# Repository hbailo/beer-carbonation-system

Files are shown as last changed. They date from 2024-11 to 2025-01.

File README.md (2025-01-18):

# Sistema de carbonatación de cerveza

## Alumno
Hernán Leandro Bailo

## Resumen
Se describe el desarrollo de la automatización de un sistema de carbonatación de cerveza en barriles.

El sistema se basa en una placa de desarrollo NUCLEO-F429ZI y esta diseñado conforme a los patrones de
diseño de procesos modulares de ISA S88.

Entre sus funcionalidades principales se incluye el control mediante HMI de la receta de carbonatación, per-
mitiendo al operador iniciar, detener y reanudar su ejecución, el monitoreo y control mediante una computadora
de supervisión y el acceso a los datos de procesos desde un navegador web.

El sistema destaca por su capacidad para mejorar la consistencia en la calidad del producto final, optimizando
el tiempo de operación y minimizando la intervención manual. Su diseño modular y escalable lo convierte en una
solución adaptable para diferentes escalas de producción en la industria cervecera.

## Descripción del proceso
En el proceso de elaboración de cerveza una de las últimas etapas es la carbonatación, donde se incorpora
dióxido de carbono a lı́quido para crear efervescencia, realzar el sabor, conservar la cerveza y otros propósitos.
En el caso actual la carbonatación se realiza artificialmente mediante la incorporación forzada del gas.

El diagrama P&ID del sistema de carbonatación se muestra a continuación. Los tags utilizados están en formato IEC 81346 [1].

El sistema consiste en untanque de CO2 conectado a un barril de cerveza a través de la válvula solenoide
QMB1. El barril se encuentra montado sobre una criba vibratoria que se acciona mediante el motor eléctrico
MAA1. La presión interna del barril se mide con el transmisor BPA1.

<picture>
    <source media="(prefers-color-scheme: dark)" srcset="doc/architecture/process-and-instrumentation-diagram-dark.png">
    <source media="(prefers-color-scheme: light)" srcset="doc/architecture/process-and-instrumentation-diagram-light.png"> 
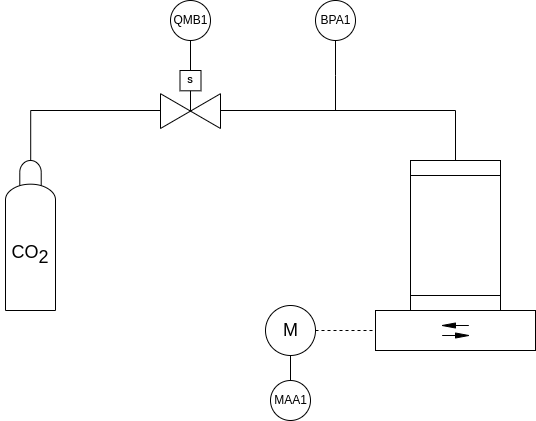
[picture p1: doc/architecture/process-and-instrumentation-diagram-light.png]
Shows the recipe state diagram.
    
</picture>

### Fases del proceso
El procedimiento de carbonatación se basa en la iteración de las siguientes dos fases, estructuradas según el patrón de diseño ISA S88 [2]:

* Inyección de CO2: Accionando la válvula solenoide (normalmente cerrada) (QMB1) se inyecta CO2 al barril
de cerveza. La cantidad de gas inyectado se mide a través de la presión del barril (BPA1).

* Disolución del CO2: Encendiendo la criba vibratoria (MAA1) se agita la cerveza y se favorece la disolución
del CO2. El grado de disolución se mide indirectamente a través de la presión del barril (BPA1). A medida
que el CO2 se diluye en la cerveza BPA1 decrece y se establece en un determinado valor. Se asume que se
completó la disolución cuando dos muestras sucesivas de BPA1 con una separación de 1s difieren en menos
de 10 mbar.

### Receta de carbonatación
La receta que se requiere automatizar para lograr la carbonatación completa de un barril estándar se describe
a continuación en pasos numerados y se muestra gráficamente en el diagrama de flujo siguiente.

1. Se inyecta CO2 al barril accionando QMB1 hasta que BPA1 = 3 bar.
2. Se diluye el CO2 encendiendo la criba vibratoria. Si una vez diluido el gas se mide 0,9 bar < BPA1 < 1 bar
entonces se finaliza la receta con el barril correctamente carbonatado, sino si BPA1 < 0,9 bar se pasa al
paso 3.
3. Se inyecta CO2 al barril accionando QMB1 hasta que BPA1 = 2 bar.
4. Se diluye el CO2 y si 0,9 bar < BPA1 < 1 bar se finaliza satisfactoriamente la receta, sino si BPA1 < 0,9 bar
se pasa al paso 5.
5. Se inyecta CO2 al barril accionando QMB1 hasta que BPA1 = 1 bar.
6. Se diluye el CO2 y si 0,9 bar < BPA1 < 1 bar se finaliza satisfactoriamente la receta, sino si BPA1 < 0,9 bar
se repiten los pasos 5 y 6 indefinidamente.
En los pasos 2, 4 y 6 la condición BPA1 > 1 bar detiene la receta dado que no deberı́a producirse si el sistema
funciona adecuadamente. Se debe revisar el equipo.

Nota: en los pasos 2, 4 y 6 la condición BPA1 > 1 bar detiene la receta dado que no debería producirse si el sistema funciona adecuadamente. Se debe revisar el equipo.

<picture>
    <source media="(prefers-color-scheme: dark)" srcset="doc/design/classes/CarbonationRecipe/recipe-flow-diagram-dark.png">
    <source media="(prefers-color-scheme: light)" srcset="doc/design/classes/CarbonationRecipe/recipe-flow-diagram-light.png"> 
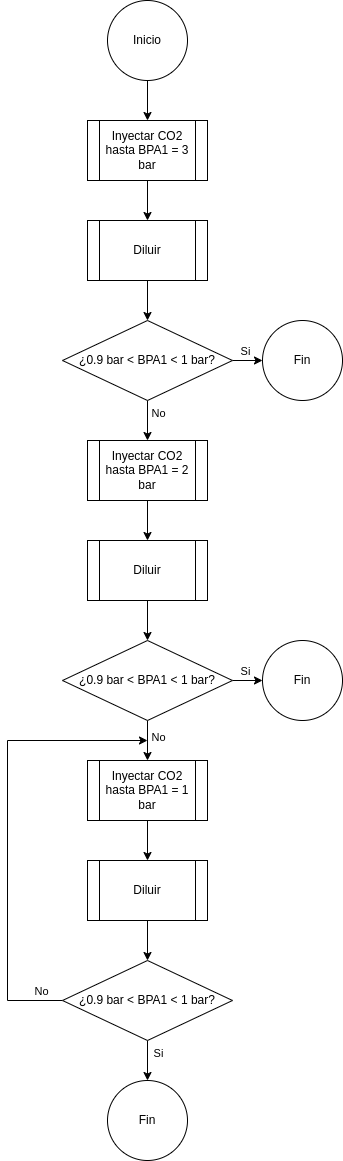
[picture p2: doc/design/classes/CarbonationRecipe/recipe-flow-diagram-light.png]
Shows the recipe flow diagram.
    
</picture>

### Operación
La operación del sistema se basa en la ejecución de la receta de carbonatación, siguiendo el patrón de diseño de manufactura flexible ISA S88 [2].

El operador controla el estado de la receta a través de los siguientes comandos:

* Start:  inicia la receta.
* Stop:   detiene la receta.
* Hold:   pausa la receta.
* Resume: reanuda la receta.
* Reset:  reinicia la receta.

Los comandos se encuentran ligados con los estados de la receta de acuerdo al siguiente diagrama:

<picture>
    <source media="(prefers-color-scheme: dark)" srcset="doc/design/classes/CarbonationRecipe/recipe-state-diagram-dark.png">
    <source media="(prefers-color-scheme: light)" srcset="doc/design/classes/CarbonationRecipe/recipe-state-diagram-light.png"> 
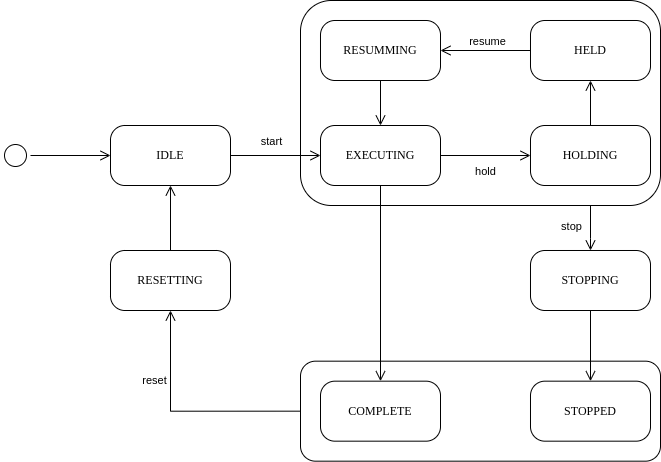
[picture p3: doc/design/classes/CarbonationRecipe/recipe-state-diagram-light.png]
Shows the recipe state diagram.
    
</picture>

### Alarmas y acciones de protección
* BPA1 > 4 bar: se detiene el proceso, se indica la alarma en el HMI, se activa la sirena y se envía un mensaje a la computadora de supervisión.

## Arquitectura de control
A continuación se muestra un esquemático de los módulos de hardware del sistema y se procede con las especificaciones de los mismos.

<picture>
    <source media="(prefers-color-scheme: dark)" srcset="doc/architecture/hardware-architecture-dark.png">
    <source media="(prefers-color-scheme: light)" srcset="doc/architecture/hardware-architecture-light.png"> 
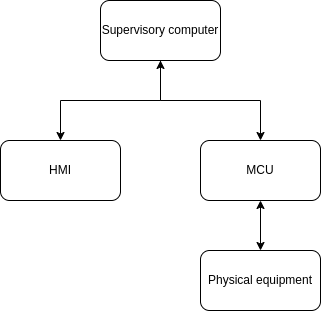
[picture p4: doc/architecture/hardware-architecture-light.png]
Shows the hardware architecture.
    
</picture>

### Microcontrolador
El control del sistema se realiza con una placa NUCLEO-F429ZI que posee el microcontrolador STM32F249ZI.

#### Periféricos
* DIGITAL OUT 1: Señal de actuación de la válvula solenoide QMB1.
* DIGITAL OUT 2: Señal de actuación del motor MAA1 de la criba vibratoria.
* DIGITAL OUT 3: Señal de actuación de la sirena.
* DIGITAL IN  1: Señal de display del HMI presionado. (XPT2046).
* ANALOG IN 1: Medición de presión del sensor BPA1.
* UART: Comunicación con la computadora de supervisión.
* SPI 1: Comunicación con el driver del display del HMI (ILI9341).
* SPI 2: Comunicación con el driver del touch del HMI (XPT2046).

### HMI
El operador puede monitorear y controlar el proceso desde el panel táctil.

La conexión con el microcontrolador se realiza a través de SPI. El LCD se controla a través del driver ILI9341 y la interfaz táctil con el driver XPT2046.

Se visualiza en el HMI:
* Estado actual de la receta.
* Paso actual de la receta.
* Presión interna del barril.
* Alarmas.
* Botones de comando.

Se comanda desde el HMI:
* Arranque, parada, reinicio, reanudación y pausa de la receta.
* Reconocimiento de alarmas.

### Computadora de supervisión
El operador puede obtener monitorear y controlar el proceso desde la computadora de supervisión.

La conexión se realiza a través de UART.

Datos monitoreables:
* Presión del barril.

NOTA: Los datos reportados se envían en formato JSON.

Comandos permitidos:
* Arranque, parada, reinicio, reanudación y pausa de la receta.
* Reconocimiento de alarmas.

## Software

### Arquitectura

#### Diagrama UML de clases

<picture>
    <source media="(prefers-color-scheme: dark)" srcset="doc/architecture/uml-dark.png">
    <source media="(prefers-color-scheme: light)" srcset="doc/architecture/uml-light.png"> 
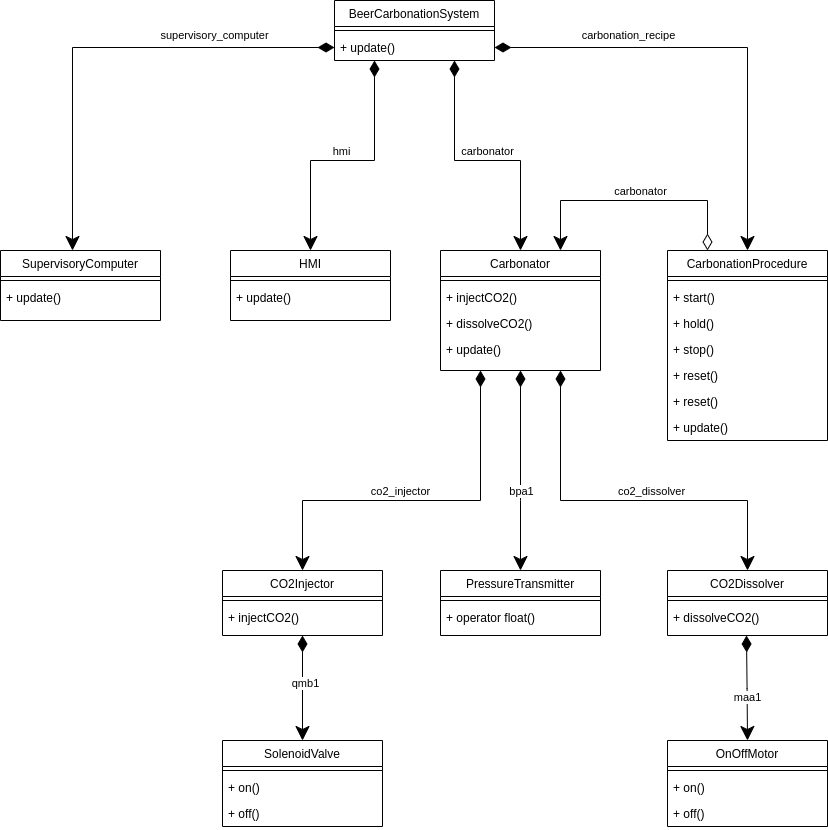
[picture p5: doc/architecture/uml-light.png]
Shows the UML class diagram of the architecture.
    
</picture>

#### Diagramas de estados
A continuación se muestran los principales diagramas de estados de las clases.

La clase CarbonationRecipe permite el control del estado de la receta de carbonatación implementando la siguiente máquina de estados:

<picture>
    <source media="(prefers-color-scheme: dark)" srcset="doc/design/classes/CarbonationRecipe/recipe-state-diagram-dark.png">
    <source media="(prefers-color-scheme: light)" srcset="doc/design/classes/CarbonationRecipe/recipe-state-diagram-light.png"> 
    Shows the state diagram of the CarbonationRecipe class.
</picture>

Dentro del estado EXECUTING se encuentra la máquina de estados que implementa la receta por pasos:

<picture>
    <source media="(prefers-color-scheme: dark)" srcset="doc/design/classes/CarbonationRecipe/recipe-step-diagram-dark.png">
    <source media="(prefers-color-scheme: light)" srcset="doc/design/classes/CarbonationRecipe/recipe-step-diagram-light.png"> 
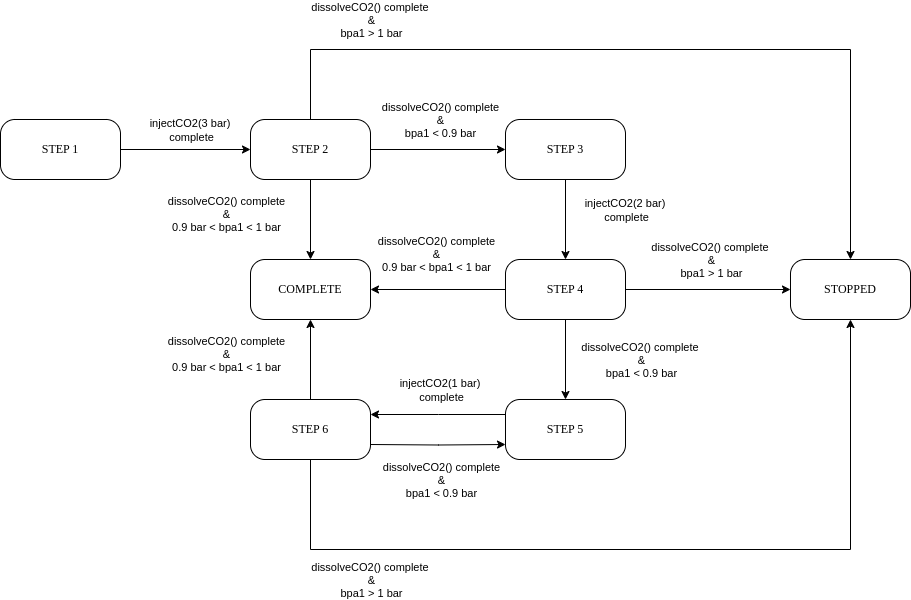
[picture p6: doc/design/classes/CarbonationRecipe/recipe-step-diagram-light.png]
Shows the step state diagram of the CarbonationRecipe class.
    
</picture>

De igual manera las clases CO2Dissolver y CO2Injector implementan la misma máquina de estados para controlar el equipo de acuerdo al estado de la receta pero cada una implementa en el estado EXECUTING el algoritmo correspondiente.

Para CO2Injector se implementa:

<picture>
    <source media="(prefers-color-scheme: dark)" srcset="doc/design/classes/CO2Injector/flowchart-diagram-dark.png">
    <source media="(prefers-color-scheme: light)" srcset="doc/design/classes/CO2Injector/flowchart-diagram-light.png"> 
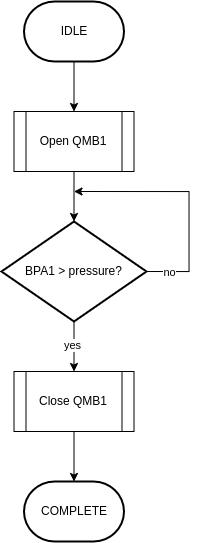
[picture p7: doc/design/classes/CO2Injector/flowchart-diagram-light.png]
Shows the flowchart of the CO2Injector phase logic.
    
</picture>

Para CO2Dissolver se implementa:

<picture>
    <source media="(prefers-color-scheme: dark)" srcset="doc/design/classes/CO2Dissolver/flowchart-diagram-dark.png">
    <source media="(prefers-color-scheme: light)" srcset="doc/design/classes/CO2Dissolver/flowchart-diagram-light.png"> 
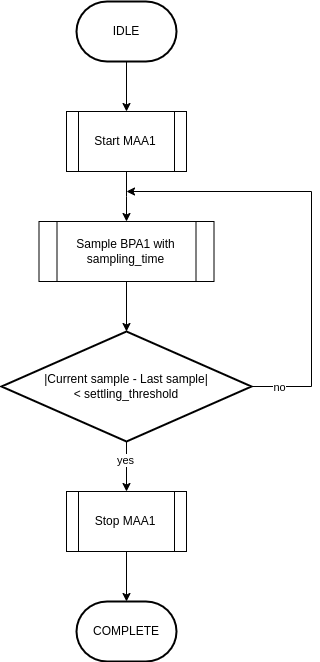
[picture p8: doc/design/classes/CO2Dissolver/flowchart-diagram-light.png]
Shows the flowchart of the CO2Dissolver phase logic.
    
</picture>

Las clases OnOffMotor y SolenoidValve son los módulos de control de los actuadores. Dado que se trata de controles on/off ambos módulos implementan la siguiente máquina de estados:

<picture>
    <source media="(prefers-color-scheme: dark)" srcset="doc/design/classes/SolenoidValve/state-diagram-dark.png">
    <source media="(prefers-color-scheme: light)" srcset="doc/design/classes/SolenoidValve/state-diagram-light.png"> 
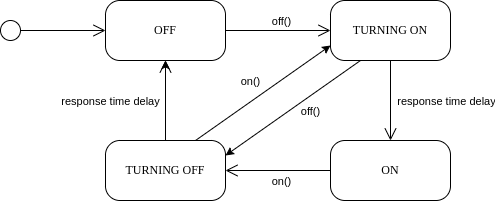
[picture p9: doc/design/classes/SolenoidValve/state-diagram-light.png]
Shows the SolenoidValve state diagram.
     
</picture>

La clase HMI se encarga de la interacción con el operador a través del display táctil. Para la gestión de la interfaz táctil implementa la máquina de estados del diagrama que se muestra a continuación. Las transiciones se basa en los eventos de pantalla presionada, pantalla liberada e interacción procesada.

<picture>
    <source media="(prefers-color-scheme: dark)" srcset="doc/design/classes/HMI/touch-state-diagram-dark.png">
    <source media="(prefers-color-scheme: light)" srcset="doc/design/classes/HMI/touch-state-diagram-light.png"> 
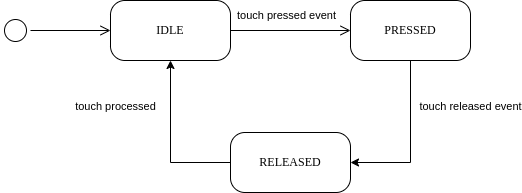
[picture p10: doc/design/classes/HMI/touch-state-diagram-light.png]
Shows the HMI touch state diagram.
     
</picture>

### Documentación
La documentación del código se ha generado con Doxygen.

Prerequisistos:
* Doxygen >= 1.9.4

Para generar la documentación, ejecutar:

```console
    doxygen Doxyfile 
```

Los archivos generados se encuentran en la carpeta `doc/doxygen`. Para visualizar la documentación en el navegador web, abrir el archivo `index.html` en `doc/doxygen/html`.

### Compilación 
Prerequisitos:
* Git >= 2.39
* CMake >= 3.19
* Python >= 3.6
* Mbed CLI 2 (mbed-tools) >= 7.59
* Arm GNU toolchain >= 12.2

1. Clonar el repositorio:

```console
    git clone https://github.com/hbailo/beer-carbonation-system.git
```

2. Inicializar y actualizar la librería mbed-os configurada como submodulo del repositorio:

```console
    git submodule init
    git submodule update --depth 1
```

3. Configurar el proyecto de Mbed con el dispositivo NUCLEO-F429ZI, la toolchain Arm GNU y el perfil develop (o debug o release, de acuerdo a lo que se necesite):

```console
    mbed-tools configure --mbed-os-path lib/mbed-os -m NUCLEO_F429ZI -b develop -t GCC_ARM -o build/develop
```

4. Generar el build system del proyecto. En caso de necesitar utilizar un entorno virtual de python definir el directorio raíz de la instalación agregando la opción `-DPython3_ROOT_DIR=path/to/venv/bin` al comando.

```console
    cmake -S . -B build/develop
```

5. Construir el proyecto. Como resultado se obtiene el binario del proyecto `beer-carbonation-system.bin` en `build/develop`.

```console
    cmake --build build/develop -j 4
```

En caso de modificarse el archivo mbed_app.json se debe repetir del paso 3 en adelante. Para todo el resto de modificaciones basta con repetir los pasos 4 y 5. 

En el archivo Makefile se encuentra un script para simplificar el proceso reiterativo de compilación en caso de contar con el programa Make. Para configurar el proyecto, ejecute:

```console
    make configure
```

y luego para construir el proyecto:

```console
    make
```

El binario producido `beer-carbonation-system.bin` se encuentra en `build/develop`.

## Referencias
[1] International Electrotechnical Commission. *IEC 81346-2:2019: Industrial systems, installations and equipment and industrial products — Structuring principles and reference designations — Part 2: Classification of objects and codes for classes.* (IEC, 2019)

[2] Brandl, Dennis. *Design Patterns for Flexible Manufacturing.* (ISA, 2007)

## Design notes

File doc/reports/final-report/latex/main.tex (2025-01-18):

\documentclass{report}

% Packages import
\usepackage[spanish, es-tabla]{babel}
\usepackage{float}
\usepackage[a4paper, left=20mm, right=18mm, top=20mm, bottom=22.5mm, footskip=15mm]{geometry}
\usepackage{graphicx}
\usepackage{hyperref}
\usepackage[utf8]{inputenc}
\usepackage{multirow}
\usepackage[table,xcdraw]{xcolor}

% Document
\begin{document}

\input{caratula/caratula}

\input{resumen/resumen}

\tableofcontents
\newpage

\section*{Registro de versiones}
\input{registro-de-versiones/registro-de-versiones}
\newpage

\chapter{Introducción general}
\input{introduccion-general/introduccion-general}

\chapter{Introducción específica}
\input{introduccion-especifica/introduccion-especifica}

\chapter{Diseño e implementación}
\input{diseño-e-implementacion/diseño-e-implementacion}

\chapter{Ensayos y resultados}
\input{ensayos-y-resultados/ensayos-y-resultados}

\chapter{Conclusiones}
\input{conclusiones/conclusiones}

\input{referencias/referencias}

\end{document}

%%% Local Variables:
%%% mode: LaTeX
%%% TeX-master: t
%%% End:

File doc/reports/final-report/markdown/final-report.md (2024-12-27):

# Memoria del Trabajo Final: Sistema Carbonatador de Cerveza

<picture>
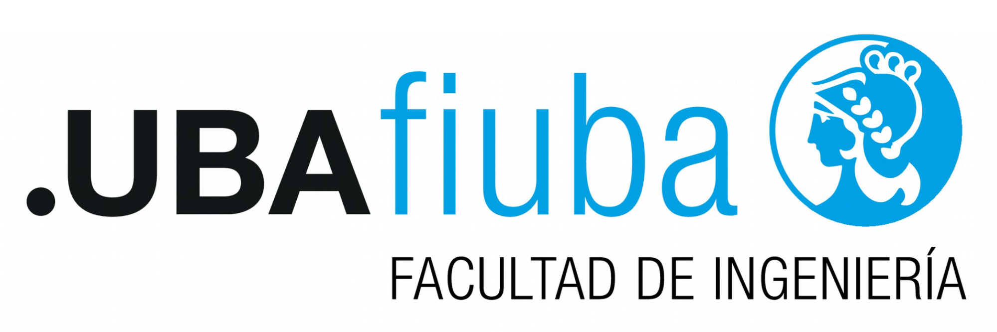
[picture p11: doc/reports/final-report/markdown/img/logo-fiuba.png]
    
</picture>

**Universidad de Buenas Aires**
**Facultad de Ingeniería**
**86.65 Sistemas Embebidos**

**Autor:** Hernán Leandro Bailo

**Padrón:** 97841

*Este trabajo fue realizado en la Ciudad de Buenos Aires entre Julio y Diciembre de 2024.*

## Resumen
Se describe el desarrollo de la automatización de un sistema de carbonatación de cerveza en barriles.

El sistema se basa en una placa de desarrollo NUCLEO-F429ZI y esta diseñado conforme a los patrones de
diseño de procesos modulares de ISA S88.

Entre sus funcionalidades principales se incluye el control mediante HMI de la receta de carbonatación, per-
mitiendo al operador iniciar, detener y reanudar su ejecución, el monitoreo y control mediante una computadora
de supervisión y el acceso a los datos de procesos desde un navegador web.

El sistema destaca por su capacidad para mejorar la consistencia en la calidad del producto final, optimizando
el tiempo de operación y minimizando la intervención manual. Su diseño modular y escalable lo convierte en una
solución adaptable para diferentes escalas de producción en la industria cervecera.

## Registro de versiones

| **Revisión** | **Cambios realizados** |  **Fecha** |
|:---:|:---:|:---:|
| 1 | Creación del documento | 12/12/2024 |
| 2 | | |
| 3 | | |

## Capítulo 1. Introducción general

### 1.1. Objetivo
  El objetivo del proyecto es desarrollar un sistema automatizado y modular de un equipo carbonatador existente para la carbonatación de cerveza en barriles, capaz de garantizar calidad, precisión y consistencia en el proceso, bajo estándares industriales como ISA S88 [1], y con capacidad de integración en sistemas de gestión mediante comunicación abierta.

### 1.2. Equipo
El equipo carbonatador a automatizar está diseñado a medida para una planta de bajo nivel de producción.
En la figura 1.1 se muestra un diagrama P&ID con tags en formato IEC 81346-2 [3].
El sistema consiste en untanque de CO2 conectado a un barril de cerveza a través de la válvula solenoide
QMB1. El barril se encuentra montado sobre una criba vibratoria que se acciona mediante el motor eléctrico
MAA1. La presión interna del barril se mide con el transmisor BPA1.

<picture>
    
</picture>

**Figura 1.1: P&ID del carbonatador.**

### 1.3. Descripción del proceso
En el proceso de elaboración de la cerveza una de las últimas etapas es la carbonatación, donde se incorpora
dióxido de carbono a lı́quido para crear efervescencia, realzar el sabor, conservar la cerveza y otros propósitos.
En el caso actual la carbonatación se realiza artificialmente mediante la incorporación forzada del gas.
El procedimiento se basa en la iteración de las siguientes dos fases, estructuradas según el patrón de diseño
ISA S88 [1]:

* Inyección de CO2: Accionando la válvula solenoide (normalmente cerrada) (QMB1) se inyecta CO2 al barril
de cerveza. La cantidad de gas inyectado se mide a través de la presión del barril (BPA1).

* Disolución del CO2: Encendiendo la criba vibratoria (MAA1) se agita la cerveza y se favorece la disolución
del CO2. El grado de disolución se mide indirectamente a través de la presión del barril (BPA1). A medida
que el CO2 se diluye en la cerveza BPA1 decrece y se establece en un determinado valor. Se asume que se
completó la disolución cuando dos muestras sucesivas de BPA1 con una separación de 1s difieren en menos
de 10 mbar.

#### 1.3.1. Receta

La receta que se requiere automatizar para lograr la carbonatación completa de un barril estándar se describe
a continuación en pasos numerados y se muestra gráficamente en el diagrama de flujo de la figura 1.2.

1. Se inyecta CO2 al barril accionando QMB1 hasta que BPA1 = 3 bar.
2. Se diluye el CO2 encendiendo la criba vibratoria. Si una vez diluido el gas se mide 0,9 bar < BPA1 < 1 bar
entonces se finaliza la receta con el barril correctamente carbonatado, sino si BPA1 < 0,9 bar se pasa al
paso 3.
3. Se inyecta CO2 al barril accionando QMB1 hasta que BPA1 = 2 bar.
4. Se diluye el CO2 y si 0,9 bar < BPA1 < 1 bar se finaliza satisfactoriamente la receta, sino si BPA1 < 0,9 bar
se pasa al paso 5.
5. Se inyecta CO2 al barril accionando QMB1 hasta que BPA1 = 1 bar.
6. Se diluye el CO2 y si 0,9 bar < BPA1 < 1 bar se finaliza satisfactoriamente la receta, sino si BPA1 < 0,9 bar
se repiten los pasos 5 y 6 indefinidamente.
En los pasos 2, 4 y 6 la condición BPA1 > 1 bar detiene la receta dado que no deberı́a producirse si el sistema
funciona adecuadamente. Se debe revisar el equipo.

<picture>
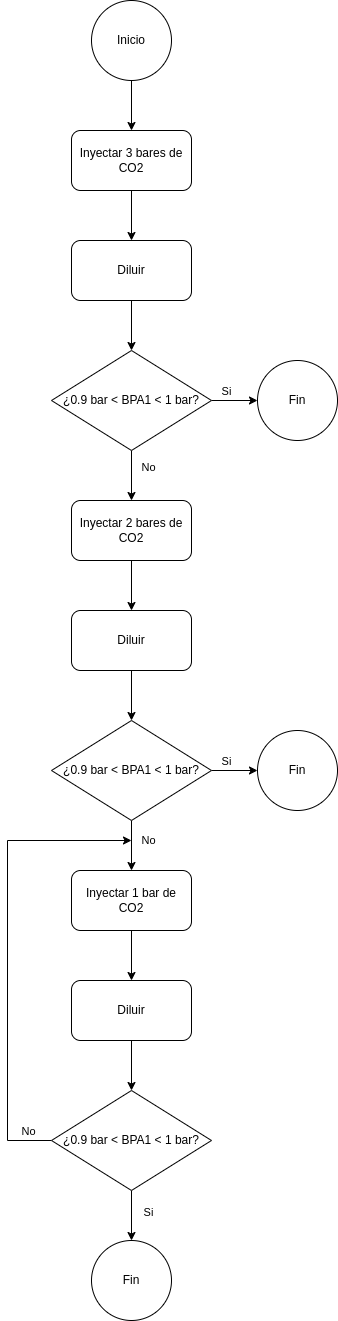
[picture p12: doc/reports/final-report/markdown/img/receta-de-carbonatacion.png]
    
</picture>

**Figura 1.2: Diagrama de flujo de la receta de carbonatación.**

#### 1.3.2. Interacción del operador

La operación del sistema se basa en la ejecución de la receta de carbonatación, siguiendo el patrón de diseño
de manufactura flexible ISA S88 [1].
El operador controla el estado de la receta a través de los siguientes comandos:

* Start: inicia la receta.
* Stop: detiene la receta.
* Hold: pausa la receta.
* Resume: reanuda la receta.
* Reset: reinicia la receta.

Los comandos se encuentran ligados con los estados de la receta de acuerdo al diagrama de estados de la
figura 1.3.

<picture>
    
</picture>

**Figura 1.3: Diagrama de estados de la ejecución de la receta de carbonatación.**

### 1.4. Arquitectura de control

El sistema de automatización se basa en una arquitectura de control tı́pica como se muestra en la figura
1.4. Consta de un único controlador controlando el equipo fı́sico, un HMI para operar y el soporte para una
computadora de supervisión con la capacidad de monitorear el proceso, a través de una conexión serie o mediante
un navegador web.

<picture>
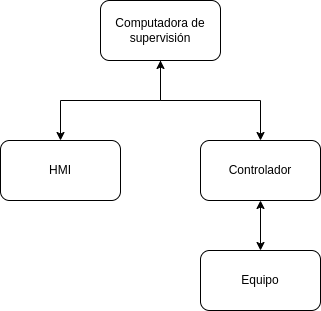
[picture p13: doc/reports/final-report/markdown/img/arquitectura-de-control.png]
    
</picture>

**Figura 1.4: Arquitectura de control.**

### 1.5. Análisis de sistemas similares en el mercado
En el mercado los carbonatadores que se venden son generalmente del tipo inline, para volúmenes altos
de producción. El sistema a automatizar maneja volúmenes de producción bajos y por ende el carbonatador
implementado opera directamente sobre los barriles. Sin embargo, se analizan tres sistemas de carbonatación
comerciales para comparar las caracterı́sticas de cada uno, en la tabla 1.1 se muestran los resultados de este
análisis.

Los productos analizados se pueden encontrar en los siguientes enlaces:

* [ProCarb™ Mini](https://www.probrew.com/products/procarb-mini/)
* [Pentair Carbonation Control System](https://foodandbeverage.pentair.com/en/products/pentair-carbonation-control-system-carbo-controller-ccr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)
* [Carboblend](https://www.alfalaval.com/products/process-solutions/brewery-solutions/blending-modules/carboblend/)

<table><thead>
  <tr>
    <th>Característica</th>
    <th>ProCarb™ Mini</th>
    <th>Pentair Carbonation<br>Control System</th>
    <th>Carboblend</th>
  </tr></thead>
<tbody>
  <tr>
    <td>Automático</td>
    <td>Si</td>
    <td>Si</td>
    <td>Si</td>
  </tr>
  <tr>
    <td>HMI</td>
    <td>Si</td>
    <td>Si</td>
    <td>Si</td>
  </tr>
  <tr>
    <td>Compacto</td>
    <td>Si</td>
    <td>Si </td>
    <td>Si</td>
  </tr>
  <tr>
    <td>Medición directa<br>de CO₂</td>
    <td>Si</td>
    <td>Si</td>
    <td>Si</td>
  </tr>
  <tr>
    <td>Comunicación<br>abierta</td>
    <td>Si</td>
    <td>Si</td>
    <td>Si</td>
  </tr>
</tbody>
</table>

**Tabla 1.1: Comparación de carbonatadores comerciales.**

## Capítulo 2. Introducción específica

### 2.1. Requisitos

En la tabla 2.1 se muestran los requisitos del sistema desarrollado.

<table><thead>
  <tr>
    <th>Grupo</th>
    <th>ID</th>
    <th>Descripción</th>
  </tr></thead>
<tbody>
  <tr>
    <td rowspan="4">Control del proceso</td>
    <td>1.1</td>
    <td>Implementación de receta de carbonatación según ISA S88.</td>
  </tr>
  <tr>
    <td>1.2</td>
    <td>Inyección de CO2 mediante válvula solenoide (QMB1).</td>
  </tr>
  <tr>
    <td>1.3</td>
    <td>Disolución de CO2 mediante criba vibratoria accionada por motor eléctrico (MAA1).</td>
  </tr>
  <tr>
    <td>1.4</td>
    <td>Monitoreo de presión (BPA1).</td>
  </tr>
  <tr>
    <td rowspan="6">HMI</td>
    <td>2.1</td>
    <td>Comunicación con MCU.</td>
  </tr>
  <tr>
    <td>2.2</td>
    <td>Indicación de estado de receta.</td>
  </tr>
  <tr>
    <td>2.3</td>
    <td>Indicación de paso de receta.</td>
  </tr>
  <tr>
    <td>2.4</td>
    <td>Indicación de alarmas.</td>
  </tr>
  <tr>
    <td>2.5</td>
    <td>Indicación de presión BPA1.</td>
  </tr>
  <tr>
    <td>2.6</td>
    <td>Botones de comando de receta: start, stop, hold, resume, reset.</td>
  </tr>
  <tr>
    <td rowspan="2">Sirena</td>
    <td>3.1</td>
    <td>Conexión con MCU.</td>
  </tr>
  <tr>
    <td>3.2</td>
    <td>Configuración de la alerta sonora.</td>
  </tr>
  <tr>
    <td rowspan="4">Computadora de<br>supervisión</td>
    <td>4.1</td>
    <td>Comunicación con MCU.</td>
  </tr>
  <tr>
    <td>4.2</td>
    <td>Comandos de receta: start, stop, hold, resume, reset.</td>
  </tr>
  <tr>
    <td>4.3</td>
    <td>Comando de reporte de presión BPA1.</td>
  </tr>
  <tr>
    <td>4.4</td>
    <td>Comando de ayuda al operador.</td>
  </tr>
  <tr>
    <td rowspan="2">Sistema de alarmas y <br>enclavamientos</td>
    <td>5.1</td>
    <td>Alarma por sobrepresión cuando BPA1 &gt; 4 bar.</td>
  </tr>
  <tr>
    <td>5.2</td>
    <td>Detención del proceso por sobrepresión cuando BPA1 &gt; 4 bar.</td>
  </tr>
  <tr>
    <td rowspan="6">Servidor web</td>
    <td>6.1</td>
    <td>Comunicación WiFi con MCU.</td>
  </tr>
  <tr>
    <td>6.2</td>
    <td>Implementación de servidor HTTP.</td>
  </tr>
  <tr>
    <td>6.3</td>
    <td>Indicación de estado de receta mediante HTML.</td>
  </tr>
  <tr>
    <td>6.4</td>
    <td>Indicación de paso de receta.</td>
  </tr>
  <tr>
    <td>6.5</td>
    <td>Indicación de presión BPA1.</td>
  </tr>
  <tr>
    <td>6.6</td>
    <td>Indicación de alarmas.</td>
  </tr>
</tbody></table>

**Tabla 2.1: Requisitos del sistema automático.**

### 2.2. Casos de uso
En las tablas 2.2, 2.3 y 2.4 se presentan tres casos de uso del sistema representativos de su funcionalidad.

<table><thead>
  <tr>
    <th>Caso de uso</th>
    <th>Inicio de receta de carbonatación</th>
  </tr></thead>
<tbody>
  <tr>
    <td>Descripción</td>
    <td>El operador inicia la receta para carbonatar un barril de cerveza.</td>
  </tr>
  <tr>
    <td>Precondición</td>
    <td>La receta debe estar en el estado Idle y el sistema no debe estar enclavado.</td>
  </tr>
  <tr>
    <td>Flujo principal</td>
    <td>1. El operador selecciona Start en el HMI.<br>2. El sistema inicia la receta.<br>3. Se inyecta CO2 y se agita el barril según el algoritmo.</td>
  </tr>
  <tr>
    <td>Flujo alternativo</td>
    <td>Si se detecta BP A1 &gt; 4 bar, se activa la alarma, se detiene el proceso y se<br>notifica al operador.</td>
  </tr>
</tbody>
</table>

**Tabla 2.2: Caso de uso 1, inicio de la ejecución de la receta.**

<table><thead>
  <tr>
    <th>Caso de uso</th>
    <th>Pausa y reanudación de receta</th>
  </tr></thead>
<tbody>
  <tr>
    <td>Descripción</td>
    <td>El operador pausa temporalmente la receta en ejecución y luego la reanuda.</td>
  </tr>
  <tr>
    <td>Precondición</td>
    <td>La receta debe estar en el estado Executing.</td>
  </tr>
  <tr>
    <td>Flujo principal</td>
    <td>1. El operador selecciona Hold en el HMI.<br>2. El sistema detiene la operación de los actuadores.<br>3. Posteriormente, selecciona Resume para continuar.</td>
  </tr>
  <tr>
    <td>Flujo alternativo</td>
    <td>Si la presión en el barril cambia mientras está pausado,<br>se realiza una notificación visual en el HMI.<br></td>
  </tr>
</tbody>
</table>

**Tabla 2.3: Caso de uso 2, pausa y reanudación de receta.**

<table><thead>
  <tr>
    <th>Caso de uso</th>
    <th>Reporte de presión BPA1 a la computadora de supervisión.</th>
  </tr></thead>
<tbody>
  <tr>
    <td>Descripción</td>
    <td>El operador se conecta a la computadora de supervisión comandando el<br>reporte de la presión BPA1.</td>
  </tr>
  <tr>
    <td>Precondición</td>
    <td>La computadora de supervisión debe estar conectada a la interfaz UART.</td>
  </tr>
  <tr>
    <td>Flujo principal</td>
    <td>1. El operador envı́a el comando ’r’ para inicial el reporte de la presión.<br>2. Se envı́a la presión BPA1 en un payload de JSON.<br>3. El operador envı́a el comando ’R’ para detener el reporte de la presión.</td>
  </tr>
  <tr>
    <td>Flujo alternativo</td>
    <td>-</td>
  </tr>
</tbody>
</table>

**Tabla 2.4: Caso de uso 3, reporte de presión BPA1 a la computadora de supervisión a través del terminal serie.**

### 2.3. Descripción de módulos utilizado
En base a la arquitectura de control y los requisitos establecidos se decidió por utilizar los módulos que se
describen a continuación.

#### 2.3.1. Módulo del microcontrolador
Se utilizó como módulo microcontrolador la placa NUCLEO-F429ZI [5], equipada con un microcontrolador
STM32F429ZI, figura 2.1.

Los principales puntos tenidos en cuenta para la adopción de esta placa son:

* Rendimiento y recursos: El STM32F429ZI incluye un núcleo ARM Cortex-M4 de alto rendimiento con
capacidad de punto flotante, ideal para realizar cálculos en tiempo real y ejecutar múltiples tareas si-
multáneamente.
* Periféricos integrados: La placa cuenta con una amplia gama de periféricos como UART, SPI, ADC y GPIO,
que permiten una integración eficiente con los sensores y actuadores del sistema.
* Compatibilidad con herramientas de desarrollo: La placa es compatible con Mbed OS y herramientas como
STM32CubeIDE, lo que facilita el desarrollo del software.
* Documentación y soporte: La disponibilidad de documentación detallada simplifica el proceso de imple-
mentación y resolución de problemas.

<picture>
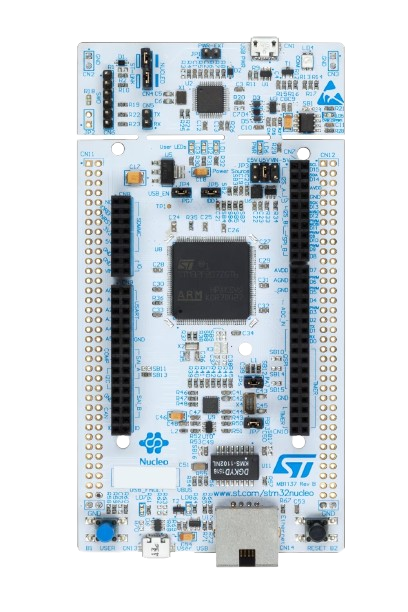
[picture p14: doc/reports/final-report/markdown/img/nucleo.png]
    
</picture>

**Figura 2.1: NUCLEO-F429ZI.**

#### 2.3.2. Módulo del display táctil
Para la implementación del HMI se utilizó el módulo display [4] con pantalla LCD TFT de 2.4’ y drivers de
hardware ILI9341 y XPT2046 que se muestra en la figura 2.2.
El comando gráfico del LCD se realiza con el hardware ILI9341 a través de una comunicación SPI y el comando
de la interacción táctil con el hardware XPT2046 también a través de una comunicación SPI.

<picture>
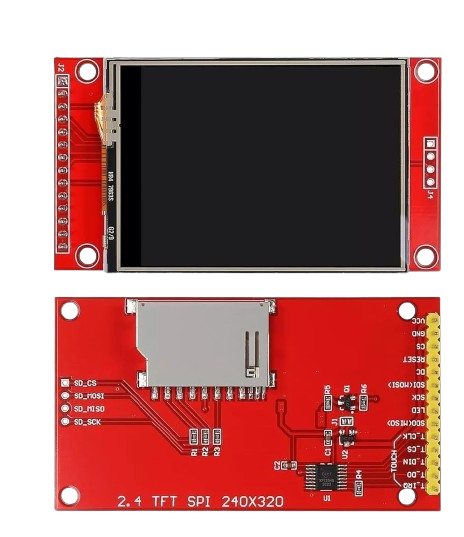
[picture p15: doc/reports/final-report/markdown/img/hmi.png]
    
</picture>

**Figura 2.2: Modulo display táctil.**

#### 2.3.3. Módulo Wi-Fi
Para la implementación de la comunicación con la computadora de supervisión a través de un navegador web
se utiliza el módulo Wi-Fi ESP01 [2] de la figura 2.3.
Este módulo se comunica con el microcontrolador a través de una interfaz UART y la configuración del mismo
se realiza a través de comandos AT.

<picture>
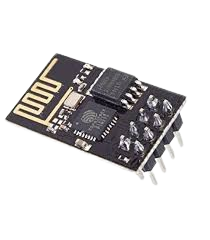
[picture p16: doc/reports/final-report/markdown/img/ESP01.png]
    
</picture>

**Figura 2.3: Modulo ESP01.**

#### 2.3.4. Buzzer
Para las indicaciones auditivas se utiliza el buzzer pasivo KY-006 que se muestra en la figura 2.4. El dispositivo
se activa enviando una señal PWM al terminal de entrada.

<picture>
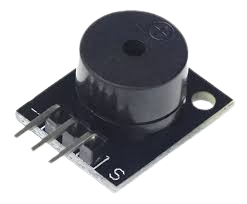
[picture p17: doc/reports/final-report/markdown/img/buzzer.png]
    
</picture>

**Figura 2.4: Buzzer.**

#### 2.3.3. Módulo de alimentación
Para la alimentación de los módulos de display, Wi-Fi y el buzzer se utiliza el módulo MB102 que se muestra
en la figura 2.5. El dispositivo genera 3,3 V al conectar el USB de entrada a 5 V .

<picture>
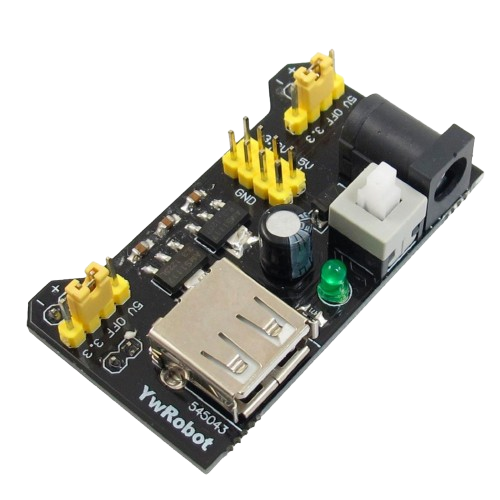
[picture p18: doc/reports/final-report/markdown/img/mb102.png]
    
</picture>

**Figura 2.5: Módulo de alimentación MB102.**

## Capítulo 3. Diseño e implementación

### 3.1.Hardware

#### 3.1.1. Diagrama en bloques
En la figura 3.1 se muestra un diagrama en bloques del hardware del sistema de automatización desarrollado.

<picture>
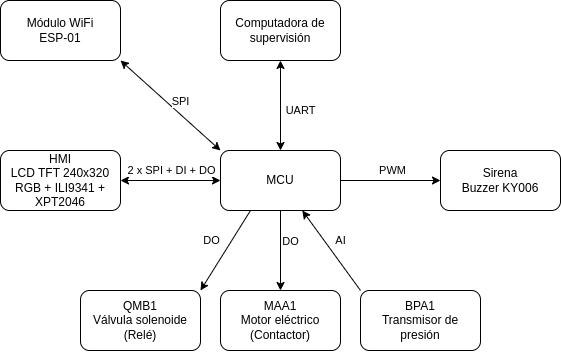
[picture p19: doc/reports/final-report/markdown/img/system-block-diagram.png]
    
</picture>

**Figura 3.1: Diagrama en bloque del sistema.**

#### 3.1.2. Lista de señales
En la tabla 3.1 se listan las señales del sistema, indicando la conexión de los puertos de la placa NUCLEO-
F429ZI a los módulos de hardware, los relé de accionamiento del motor MAA1 y la válvula QMB1 y la entrada
analógica del sensor de presión BPA1.

<table><thead>
  <tr>
    <th colspan="2">Pin del módulo de hardware</th>
    <th colspan="2">Pin de la placa Nucleo-F429ZI</th>
  </tr></thead>
<tbody>
  <tr>
    <td rowspan="6">ILI9341</td>
    <td>MISO</td>
    <td>PB4</td>
    <td>SPI1\_MISO</td>
  </tr>
  <tr>
    <td>SCKL</td>
    <td>PB3</td>
    <td>SPI1\_SCK</td>
  </tr>
  <tr>
    <td>MOSI</td>
    <td>PB5</td>
    <td>SPI1\_MOSI</td>
  </tr>
  <tr>
    <td>CS</td>
    <td>PA4</td>
    <td>SPI1\_CS</td>
  </tr>
  <tr>
    <td>DCX</td>
    <td>PC7</td>
    <td>DO</td>
  </tr>
  <tr>
    <td>RESX</td>
    <td>PA15</td>
    <td>DO</td>
  </tr>
  <tr>
    <td rowspan="5">XPT2046</td>
    <td>MISO</td>
    <td>PC2</td>
    <td>SPI2\_MISO</td>
  </tr>
  <tr>
    <td>SCKL</td>
    <td>PB13</td>
    <td>SPI2\_SCK</td>
  </tr>
  <tr>
    <td>MOSI</td>
    <td>PB15</td>
    <td>SPI2\_MOSI</td>
  </tr>
  <tr>
    <td>CS</td>
    <td>PB12</td>
    <td>SPI2\_CS</td>
  </tr>
  <tr>
    <td>PENIRQ</td>
    <td>PC6</td>
    <td>DI</td>
  </tr>
  <tr>
    <td>Siren</td>
    <td>Signal</td>
    <td>PA3</td>
    <td>PWM2/4</td>
  </tr>
  <tr>
    <td rowspan="3">ESP01</td>
    <td>Tx</td>
    <td>PD5</td>
    <td></td>
  </tr>
  <tr>
    <td>Rx</td>
    <td>PD6</td>
    <td></td>
  </tr>
  <tr>
    <td>Enable</td>
    <td>PD7</td>
    <td></td>
  </tr>
  <tr>
    <td>BPA1</td>
    <td>Signal</td>
    <td>PC0</td>
    <td>AI</td>
  </tr>
  <tr>
    <td>MAA1</td>
    <td>Relay</td>
    <td>PB0</td>
    <td>DO</td>
  </tr>
  <tr>
    <td>QMB1</td>
    <td>Relay</td>
    <td>PB7</td>
    <td>DO</td>
  </tr>
</tbody></table>

**Tabla 3.1: Lista de señales del sistema.**

#### 3.1.3. Pantalla del HMI
La pantalla del HMI implementada se muestra en la figura 3.2. A través de los botones táctiles se controla la
ejecución de la receta y con los indicadores se monitorea el estado.

<picture>
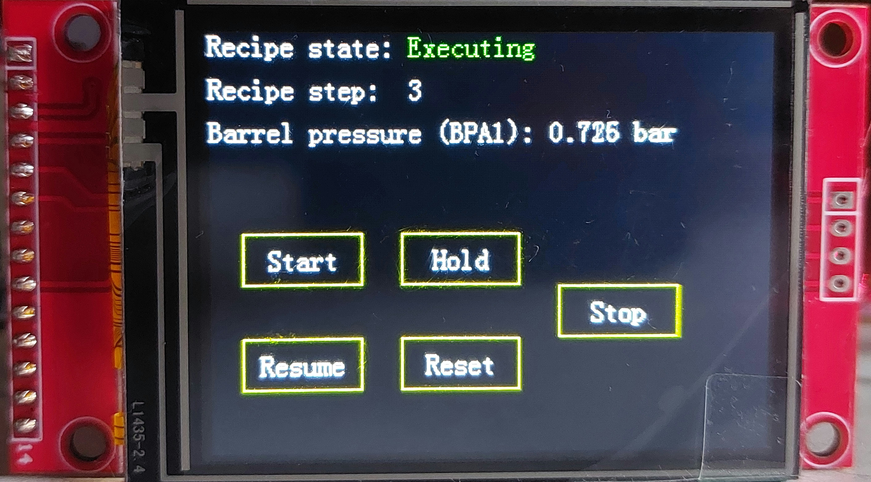
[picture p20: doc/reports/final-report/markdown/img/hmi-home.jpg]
    
</picture> 

**Figura 3.2: Pantalla del HMI.**

### 3.2. Firmware

#### 3.2.1. Repositorio
Todo el código del proyecto se encuentra en el repositorio git en [7].

#### 3.2.2. Tecnologı́a
El firmware del proyecto se desarrolla en el sistema operativo Mbed en lenguaje C++. Como compilador se
utilizó la toolchain ARM-GNU.

#### 3.2.3. Estructura del repositorio
El repositorio git se divide en las siguientes carpetas y archivos:

* doc: Documentación del proyecto.
* include: Archivos de cabecera de c++.
* lib: Bibliotecas externas. Contiene la librerı́a mbed-os como submodulo de git.
* src: Archivos fuente de c++.
* test: Archivos de soporte para pruebas de software.
* CMakeLists.txt: Archivo de compilación de cmake.
* Doxyfile: Archivo de configuración de la documentación Doxygen.
* mbed app.json: Archivo de configuración de mbed.
* mbed-os.lib: Archivo de configuración de mbed.

#### 3.2.4. Documentación
El código fuente se encuentra documentado con Doxygen, ver instrucciones en [7] para su generación. En el
presente documento se muestran detalles de alto nivel de las clases, recurrir a esta documentación en caso de
requerir mayor detalle.

#### 3.2.5. Compilación
El proyecto se compiló utilizando la toolchain de código libre ARM-GNU, ver instrucciones en [7].

#### 3.2.6. Arquitectura
En la figura 3.3 se muestra el diagrama UML del sistema. La clase contenedora es BeerCarbonationSystem.
Los módulos se comunican entre sı́ adquiriendo referencias de los objetos necesarios.

<picture>
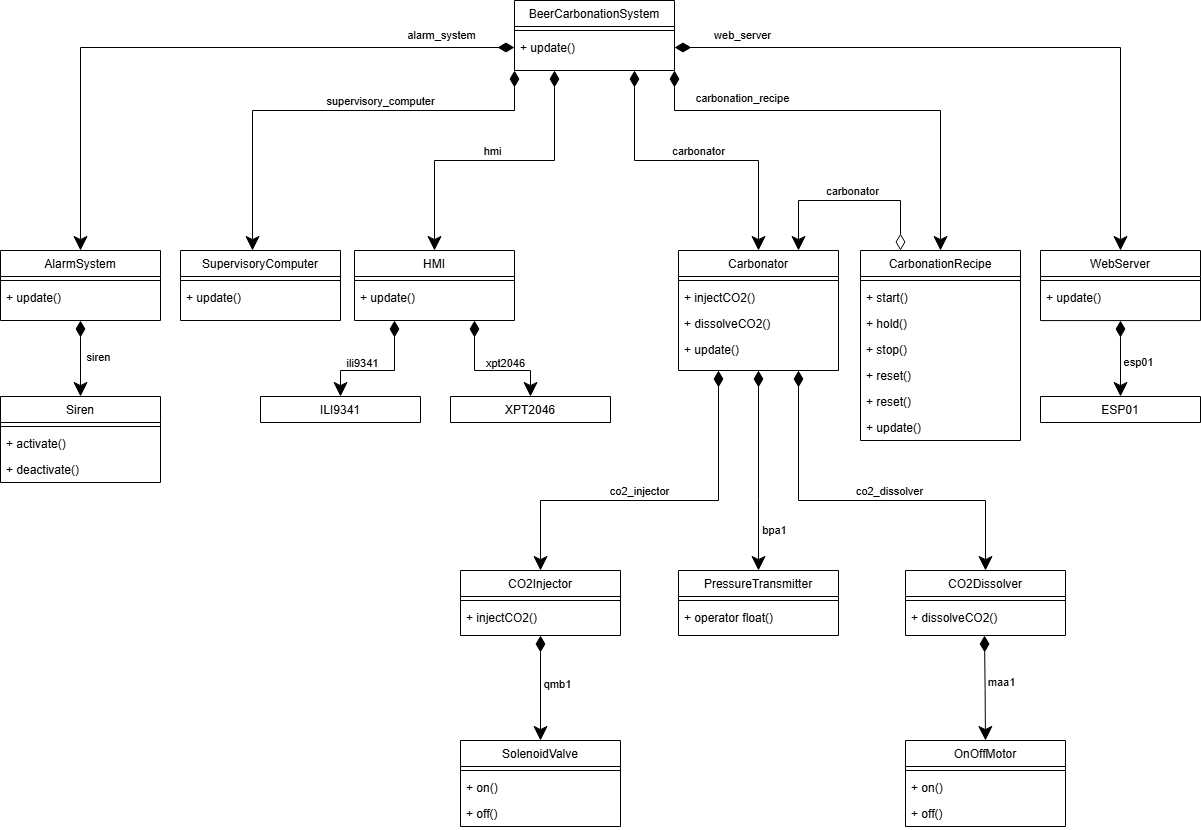
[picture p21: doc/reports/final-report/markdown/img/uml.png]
    
</picture> 

**Figura 3.3: Diagrama UML del sistema.**

#### 3.2.7. Clase BeerCarbonationSystem
La clase BeerCarbonationSystem implementa la lógica de una célula de proceso para la carbonatación de
cerveza, siguiendo el patrón de diseño ISA S88. Esta clase gestiona la interfaz de usuario, ejecuta las recetas de
carbonatación y controla los equipos relacionados con el proceso.

#### 3.2.8. Clase CarbonationRecipe
La clase CarbonationRecipe implementa la receta de carbonatación de acuerdo al patrón ISA S88, permitiendo
el control del estado de acuerdo a la máquina de estados de la figura 3.4.
Implementa el enclavamiento de protección en caso de sobrepresión BPA1 > 4 bar, deteniendo el proceso y
evitando su reanudación hasta que esta condición desaparezca.

<picture>
    
</picture> 

**Figura 3.4: Diagrama de estados de la clase CarbonationRecipe.**

Dentro del estado EXECUTING se encuentra la máquina de estados de la figura 3.5 que implementa la receta
por pasos:

<picture>
    
</picture>

**Figura 3.5: Diagrama de estados de los pasos de la receta de carbonatación.**

#### 3.2.9. Clase Carbonator
Implementa el modelo del equipo carbonatador, corresponde a una unit del modelo ISA S88. Se encarga
de propagar las señales entre los equipos de la unidad y el gestor de la receta, ofreciendo una interfaz para la
ejecución de sus fases.

#### 3.2.10. Clase CO2Injector
Implementa la fase de inyección de CO2 al barril de la figura 3.6 permitiendo configurar la presión deseada
por parámetro.

<picture>
    
</picture> 

**Figura 3.6: Diagrama de flujo de la fase de inyección de CO2.**

Internamente contiene una máquina de estados como la de la figura 3.4 que indica el estado del equipo
siguiendo el estado de la receta y una máquina de estados por pasos para implementar la lógica de la fase en el
estado EXECUTING.

#### 3.2.11. Clase CO2Dissolver
Implementa la fase de disolución de CO2 al barril de la figura 3.7.

<picture>
    
</picture> 

**Figura 3.7: Diagrama de flujo de la fase de disolución de CO2.**

Internamente contiene una máquina de estados como la de la figura 3.4 que indica el estado del equipo
siguiendo el estado de la receta y una máquina de estados por pasos para implementar la lógica de la fase en el
estado EXECUTING.

#### 3.2.12. Clase PressureTransmitter
La clase PressureTransmitter está diseñada para leer y convertir una señal analógica proveniente de un
transmisor de presión en una magnitud de presión. Utiliza un pin de entrada analógica para leer el valor de la
señal y luego escala este valor para obtener la presión en unidades de presión.

El tranmisor tiene un rango de 0 a 5 bar y produce señales de tensión de 0 a 3,3 V .

**Componentes principales:**
* pressure signal: Es un objeto de tipo AnalogIn, que representa el pin analógico al que está conectada la
señal del transmisor de presión. Se utiliza para leer el valor de la señal analógica.

#### 3.2.13. Clase OnOffMotor
La clase OnOffMotor controla un motor que puede ser encendido o apagado con un control binario. La clase
maneja los estados del motor y proporciona un control suave, gestionando los tiempos de respuesta del motor
cuando cambia entre los estados de encendido y apagado.

La máquina de estados implementada por esta clase se muestra en la figura 3.8.

<picture>
    
</picture> 

**Figura 3.8: Diagrama de estados de la clase OnOffMotor.**

**Componentes principales:**
* on actuating signal: objeto que controla el pin de salida digital conectado al motor o válvula solenoide. El
valor de este pin determina si el motor está encendido (true) o apagado (false).
* response time: El tiempo de respuesta del motor, que define cuánto tiempo tarda en cambiar de estado de
encendido o apagado. Este parámetro es útil para gestionar transiciones suaves entre los estados.

#### 3.2.14. Clase SolenoidValve
El propósito de la clase SolenoidValve es proporcionar un control sencillo y eficiente de una válvula solenoide,
permitiendo su activación o desactivación con una señal binaria. La clase asegura que las transiciones entre los
estados de la válvula (abierta y cerrada) se realicen de manera controlada, teniendo en cuenta el tiempo de
respuesta de la válvula.

La máquina de estados implementada por esta clase se muestra en la figura 3.9.

<picture>
    
</picture> 

**Figura 3.9: Diagrama de estados de la clase SolenoidValve.**

**Componentes principales:**
* on actuating signal: objeto que controla el pin de salida digital conectado al motor o válvula solenoide. El
valor de este pin determina si el motor está encendido (true) o apagado (false).
* response time: El tiempo de respuesta de la válvula solenoide, que define cuánto tiempo tarda en cambiar de
estado de encendido o apagado. Este parámetro es útil para gestionar transiciones suaves entre los estados.

#### 3.2.15. Clase AlarmSystem
La clase AlarmSystem implementa el sistema de alarmas del proceso de carbonatación. Su principal función
es monitorear las condiciones crı́ticas definidas en el proceso y activar alarmas en caso de detectar situaciones
anómalas.

El sistema incluye un registro de alarmas que se evalúan periódicamente, activando una sirena en caso de que
alguna alarma esté activa.

**Alarmas implementadas:**
* Sobrepresión del barril: Se activa cuando la presión del sensor BPA1 excede los 4

**Componentes principales:**
* Registro de alarmas: Cada alarma está definida por un mensaje descriptivo, una condición de activación
(trigger) y un estado actual (ACTIVA o INACTIVA).
* Siren: Buzzer que se activa en caso de alarmas activas.

#### 3.2.16. Clase Siren
La clase Siren controla una sirena mediante una señal PWM (Pulse Width Modulation). Permite activar o
desactivar la sirena y configurar la frecuencia de su tono. Es utilizada como un mecanismo de notificación acústica en el sistema.

**Componentes principales:**
* on actuating signal: Señal PWM utilizada para controlar la sirena.
* Frecuencia del tono: Configurable dinámicamente para ajustar el sonido emitido por la sirena.

#### 3.2.17. Clase HMI
La clase HMI gestiona la interfaz de usuario del sistema de carbonatación, controlando la pantalla LCD y la
interacción táctil para monitorear y controlar el proceso de carbonatación.

**Componentes principales:**
* LCD driver ILI9341: Se utiliza para mostrar información al usuario, como el estado de la receta, la presión
del barril y los pasos del proceso de carbonatación.
* Driver táctil XPT2046: Permite la interacción táctil del usuario con la interfaz, detectando toques y gestos
en la pantalla.

#### 3.2.18. Clase ILI9341
La clase ILI9341 es una implementación para controlar una pantalla LCD basada en el controlador ILI9341.
Utiliza una comunicación SPI para interactuar con el hardware y proporciona métodos para dibujar pı́xeles, lı́neas,
rectángulos, imágenes y llenar la pantalla con un color especı́fico. También incluye funciones de inicialización y
control de la pantalla.

**Componentes principales:**
* SPI: Interfaz de comunicación para enviar y recibir datos.
* CS (Chip Select): Pin para seleccionar el dispositivo ILI9341.
* DCX (Data/Command): Pin para indicar si se están enviando datos o comandos.
* RESX (Reset): Pin para realizar un reset hardware en la pantalla.

#### 3.2.19. Clase XPT2046
La clase XPT2046 proporciona la interfaz para interactuar con el controlador táctil de la pantalla, que utiliza
el chip XPT2046. Esta clase maneja la comunicación SPI y las interrupciones para detectar eventos táctiles, como
presionar y soltar.

**Componentes principales:**
* SPI: Interfaz de comunicación para enviar y recibir datos.
* CS (Chip Select): Pin para seleccionar el dispositivo ILI9341.
* penirq (Pin de Interrupción): Pin de interrupción que detecta eventos táctiles, como cuando la pantalla
es tocada o liberada. Utiliza una interrupción externa para activar funciones de callback definidas por el
usuario, lo que permite responder a los eventos de toque en tiempo real.
* Callback para eventos táctiles: Funciones que se ejecutan cuando se detecta que la pantalla ha sido tocada
(onTouchPressed) o cuando el toque ha sido liberado (onTouchReleased). Estas funciones son proporciona-
das por el usuario al crear el objeto de la clase XPT2046.

#### 3.2.20. Clase WebServer
La clase WebServer gestiona la comunicación entre el sistema de carbonatación y un servidor web, permitiendo
la visualización remota del estado del proceso de carbonatación a través de una interfaz web. Utiliza un módulo
ESP01 para la conexión Wi-Fi y la transmisión de información.

**Componentes principales:**
* esp01: Objeto que representa el módulo ESP01, responsable de la conexión Wi-Fi y la gestión de solicitudes
HTTP.

#### 3.2.21. Clase ESP01
La clase ESP01 gestiona la comunicación con el módulo Wi-Fi ESP01, permitiendo la conexión a una red
Wi-Fi, la recepción de solicitudes HTTP y el envı́o de respuestas. Utiliza comandos AT para interactuar con el
ESP01 y establece una conexión en modo estación, permitiendo la interacción con un servidor web.

**Componentes principales:**
* uart: Interfaz UART para la comunicación serial con el módulo ESP01, configurada a 115200 baudios.
* enable: Salida digital para habilitar o deshabilitar el módulo ESP01.

#### 3.2.22. Clase SupervisoryComputer
La clase SupervisoryComputer permite conectar un operador al sistema de carbonatación de cerveza, faci-
litando la supervisión y control remoto del proceso. A través de una interfaz UART, el operador puede enviar
comandos para iniciar, detener, pausar, reanudar o restablecer el proceso de carbonatación. Además, esta clase
permite obtener reportes en tiempo real sobre el estado del proceso, como la presión de la carbonatación, sin ser
directamente responsable de ejecutar el proceso de carbonatación en sı́.

**Componentes principales:**
* uart (Interfaz UART):La comunicación entre el operador y el sistema se realiza a través de una interfaz
UART a 9600 baudios. El operador envı́a comandos al sistema, y el sistema responde con información o
reportes, lo que permite al operador supervisar el estado del proceso. ReportingState:Esta enumeración
gestiona el estado de los reportes. Los reportes pueden estar en estado REPORTING”(enviando datos)
o ÏDLE” (sin reportar). El estado de reporte permite al operador recibir información periódica sobre el
proceso.

## Capítulo 4. Ensayos y resultados

### 4.1. Pruebas funcionales del hardware
Las pruebas funcionales del hardware se realizaron por módulos.

### 4.1.1. Módulo Wi-Fi ESP01
Se conectó el módulo a la placa y en paralelo un analizador de protocolos para verificar el correcto envı́o de
comandos y la recepción de respuestas.

### 4.1.2. Módulo HMI
Se conectó el módulo a la placa y se realizó la calibración del display mediante la graficación de puntos.
Adicoinalmente se conectó un analizador de protocolos en los pines de comunicación ambos SPI para verificar el
correcto envı́o de comandos y la recepción de respuestas.

### 4.1.3. Módulo buzzer
Se conectó el buzzer al terminal de masa y se le envı́o una señal PWM con la placa nucleo verificando el
correcto funcionamiento.

### 4.1.4. Transmisor de presión
El transmisor de presión se simuló mediante un potenciometro de 50 kΩ. Se conectó el mismo a los 3,3 V
generados por la placa y se verificó que el valor medido por el objeto AnalogIn sea consistente con las mediciones
realizadas con multı́metro.

### 4.1.5. Módulo de alimentación
Se conectó el módulo de alimentación al protoboard y a la fuente de 5 V . Se verificó mediante una medición de voltı́metro que la tensión generada era de 3,3 V.

### 4.1.6. Motor MAA1 y válvula solenoide QMB1
Para demostrar el correcto funcionamiento de las salidas digitales correspondientes al motor MAA1 y QMB1
se conectaron sus salidas a los LEDs 1 y 2 de la placa NUCLEO.

### 4.1.7. Pruebas funcionales del firmware
Las pruebas funcionales del firmware se realizaron en conjunto con las distintas pruebas para los módulos de
hardware.
La lógica de la receta se verificó mediante el uso del debugger.

### 4.1.8. Pruebas de integracion
Las pruebas de integración realizadas se encuentran en formato de video en [6].

Se verificó:
* Disposición del hardware.
* Lógica de la receta y respuesta a comandos.
* Comandos mediante la computadora de supervisión por terminal serie.
* Monitoreo mediante el servidor web.
* Alarmas y enclavamientos.

### 4.1.9. Cumplimiento de requisitos
En la tabla 4.1 se presenta la evaluación del cumplimiento de los requisitos iniciales de la tabla 2.1. Se evaluó
a el estado actual de cada uno indicando en verde aquellos que ya fueron cumplidos y en rojo los requerimientos
no cumplidos.

<picture>
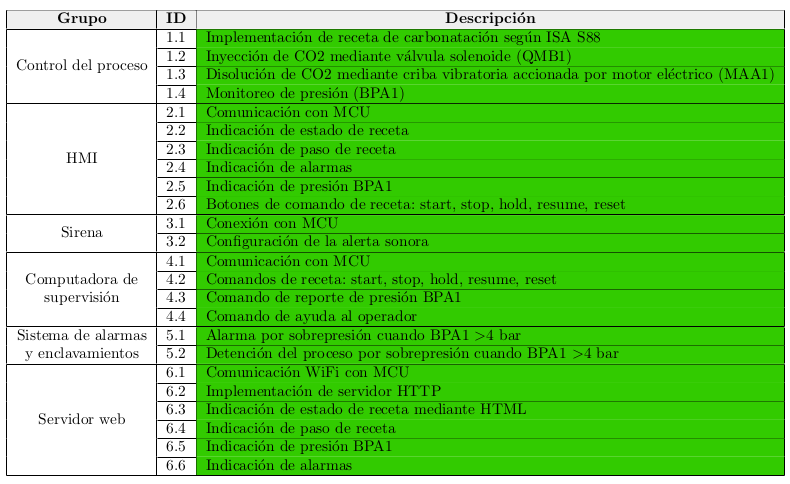
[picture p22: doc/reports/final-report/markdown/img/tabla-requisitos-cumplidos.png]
    
</picture> 

**Tabla 4.1: Estado de los requisitos.**

### 4.2. Documentación del desarrollo realizado

<table><thead>
  <tr>
    <th>Elemento</th>
    <th>Referencia</th>
  </tr></thead>
<tbody>
  <tr>
    <td>Presentación del proyecto</td>
    <td>Capı́tulo 1</td>
  </tr>
  <tr>
    <td>Listado de requisitos</td>
    <td>Tabla 2.1</td>
  </tr>
  <tr>
    <td>Casos de uso del proyecto</td>
    <td>Tablas 2.2 a 2.3</td>
  </tr>
  <tr>
    <td>Diagrama en bloques del sistema</td>
    <td>Figura 3.1</td>
  </tr>
  <tr>
    <td>Lista de señales</td>
    <td>Tabla 3.1</td>
  </tr>
  <tr>
    <td>Implementación del hardware</td>
    <td>Sección 3.1</td>
  </tr>
  <tr>
    <td>Módulos de software</td>
    <td>Sección 3.2</td>
  </tr>
  <tr>
    <td>Repositorio</td>
    <td>[7]</td>
  </tr>
  <tr>
    <td>Cumplimiento de requisitos</td>
    <td>Tabla 4.1</td>
  </tr>
  <tr>
    <td>Conclusiones finales</td>
    <td>Capı́tulo 5</td>
  </tr>
</tbody>
</table>

**Tabla 4.2: Elementos del sumario del sistema automático para el sistema de carbonatación de cerveza.**

## Capı́tulo 5 Conclusiones

### 5.1. Resultados obtenidos
El sistema desarrollado en base al patrón de diseño de ISA S88 resulta mantenible, escalable y extensible.
Por otro lado, implementar el proyecto en mbed aceleró los tiempos de desarrollo pero significó una perdida
de dominio en cuanto a conocimiento interno del sistema operativo.

Teniendo en cuenta que el soporte para mbed finaliza en 2026 es conveniente migrar el código para utilizar
solo la libreria STM32CubeF4.

### 5.2. Próximos pasos

* Migrar el código desde mbed a la librerı́a STM32CubeF4.
* Crear un worflow con la toolchain ARM-GNU de forma de independizarse de los IDE para automatizar
tareas y lograr control total del proceso.
* Crear y automatizar pruebas unitarias y de integración mediante un esquema xUnit.
* Refactorizar la clase WebServer para gestionar mejor los tiempos de espera y la latencia de las peticiones.

## Bibliografı́a

[1] Brandl, Dennis. Design Patterns for Flexible Manufacturing. (ISA, 2007).

[2] Shenzhen Anxinke Technology CO. ESP-01 WiFi Module. (2015). Disponible en https://www.
microchip.ua/wireless/esp01.pdf al [12/12/2024].

[3] International Electrotechnical Commission. IEC 81346-2:2019: Industrial systems, installations and
equipment and industrial products — Structuring principles and reference designations — Part 2: Classifica-
tion of objects and codes for classes. (IEC, 2019).

[4] LCD wiki. 2.8inch SPI Module ILI9341 SKU:MSP2807. Disponible en http://www.lcdwiki.com/2.8inch_
SPI_Module_ILI9341_SKU:MSP2807 al [12/12/2024].

[5] ST Microelectronics. NUCLEO-F429ZI. Disponible en https://www.st.com/en/evaluation-tools/
nucleo-f429zi.html al [12/12/2024].

[6] Bailo, Hernán L.. Pruebas de integración del sistema Beer Carbonation System. Disponible en https://drive.google.com/drive/folders/1NrQh9VOOGA5issQOtzWXVuDIw9n37sIr?usp=sharing al [12/12/2024].

[7] Bailo, Hernán L.. Beer Carbonation System. Disponible en https://github.com/hbailo/beer-carbonation-system
al [12/12/2024].

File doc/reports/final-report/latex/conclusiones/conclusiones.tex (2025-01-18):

\section{Resultados obtenidos}
El sistema desarrollado en base al patrón de diseño de ISA S88 resulta mantenible, escalable y extensible.

Por otro lado, implementar el proyecto en mbed aceleró los tiempos de desarrollo pero significó una perdida de dominio en cuanto a conocimiento interno del sistema operativo.

Teniendo en cuenta que el soporte para mbed finaliza en 2026 es conveniente migrar el código para utilizar solo la libreria STM32CubeF4.

\section{Próximos pasos}

\begin{itemize}
\item Migrar el código desde mbed a la librería STM32CubeF4.
\item Crear un worflow con la toolchain ARM-GNU de forma de independizarse de los IDE para automatizar tareas y lograr control total del proceso.
\item Crear y automatizar pruebas unitarias y de integración mediante un esquema xUnit.
\item Refactorizar la clase WebServer para gestionar mejor los tiempos de espera y la latencia de las peticiones.
\end{itemize}

%%% Local Variables:
%%% mode: LaTeX
%%% TeX-master: "../main"
%%% End:

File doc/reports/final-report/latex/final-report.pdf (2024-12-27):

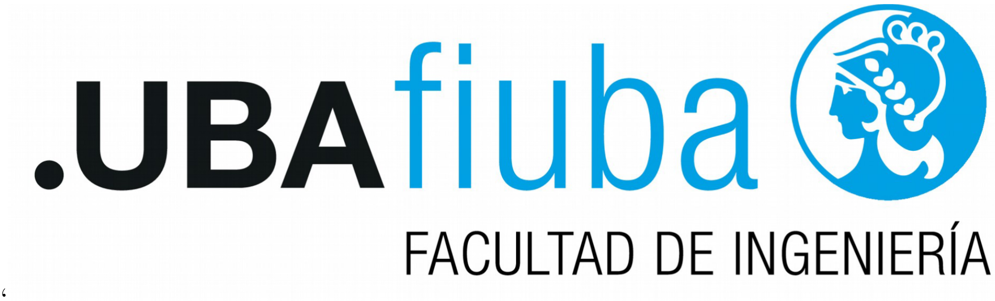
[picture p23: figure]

‘

## Universidad de Buenos Aires Facultad de Ingeniería 86.65 Sistemas Embebidos

## Memoria del Trabajo Final: Sistema Carbonatador de cerveza

## Autor: Hernán Leandro Bailo

## Legajo: 97.841

## Este trabajo fue realizado en la Ciudad de Buenos Aires entre Julio y

Diciembre de 2024.

Resumen

Se describe el desarrollo de la automatización de un sistema de carbonatación de cerveza en barriles.
El sistema se basa en una placa de desarrollo NUCLEO-F429ZI y esta diseñado conforme a los patrones de diseño de procesos modulares de ISA S88.
Entre sus funcionalidades principales se incluye el control mediante HMI de la receta de carbonatación, permitiendo al operador iniciar, detener y reanudar su ejecución, el monitoreo y control mediante una computadora de supervisión y el acceso a los datos de procesos desde un navegador web.
El sistema destaca por su capacidad para mejorar la consistencia en la calidad del producto final, optimizando el tiempo de operación y minimizando la intervención manual. Su diseño modular y escalable lo convierte en una solución adaptable para diferentes escalas de producción en la industria cervecera.

´

# Indice general

1. Introducción general | 4
2. Introducción específica | 9
3. Diseño e implementación | 14

4. Ensayos y resultados | 24
5. Conclusiones | 27

## Registro de versiones

Revisión | Cambios realizados | Fecha
1 | Creación del documento | 12/12/2024

# Capítulo 1

# Introducción general

## 1.1. Objetivo

El objetivo del proyecto es desarrollar un sistema automatizado y modular de un equipo carbonatador existente para la carbonatación de cerveza en barriles, capaz de garantizar calidad, precisión y consistencia en el proceso, bajo estándares industriales como ISA S88 [1], y con capacidad de integración en sistemas de gestión mediante comunicación abierta.

## 1.2. Equipo

El equipo carbonatador a automatizar esta diseñado a medida para una planta de bajo nivel de producción. En la figura 1.1 se muestra un diagrama P&ID con tags en formato IEC 81346-2 [3].
El sistema consiste en untanque de CO2 conectado a un barril de cerveza a través de la válvula solenoide QMB1. El barril se encuentra montado sobre una criba vibratoria que se acciona mediante el motor eléctrico MAA1. La presión interna del barril se mide con el transmisor BPA1.

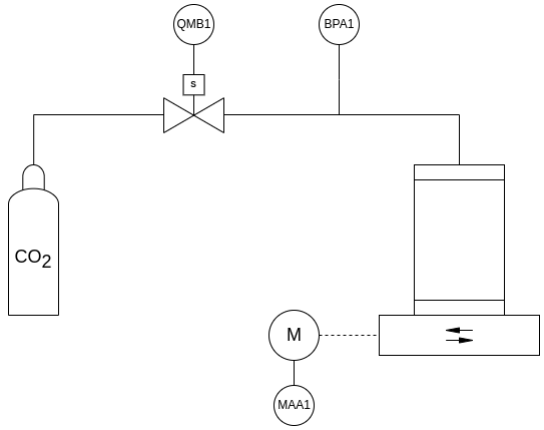
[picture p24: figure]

Figura 1.1: P&ID del carbonatador

## 1.3. Descripción del proceso

En el proceso de elaboración de la cerveza una de las últimas etapas es la carbonatación, donde se incorpora dióxido de carbono a líquido para crear efervescencia, realzar el sabor, conservar la cerveza y otros propósitos. En el caso actual la carbonatación se realiza artificialmente mediante la incorporación forzada del gas.
El procedimiento se basa en la iteración de las siguientes dos fases, estructuradas según el patrón de diseño ISA S88 [1]:

Inyección de CO2: Accionando la válvula solenoide (normalmente cerrada) (QMB1) se inyecta CO2 al barril de cerveza. La cantidad de gas inyectado se mide a través de la presión del barril (BPA1).

Disolución del CO2: Encendiendo la criba vibratoria (MAA1) se agita la cerveza y se favorece la disolución del CO2. El grado de disolución se mide indirectamente a través de la presión del barril (BPA1). A medida que el CO2 se diluye en la cerveza BPA1 decrece y se establece en un determinado valor. Se asume que se completó la disolución cuando dos muestras sucesivas de BPA1 con una separación de 1s difieren en menos de 10 mbar.

### 1.3.1. Receta

La receta que se requiere automatizar para lograr la carbonatación completa de un barril estándar se describe a continuación en pasos numerados y se muestra gráficamente en el diagrama de flujo de la figura 1.2.

1. Se inyectan 3 bares de CO2 al barril accionando QMB1 hasta que BP A1 = 3 bar.
2. Se diluye el CO2 encendiendo la criba vibratoria. Si una vez diluido el gas se mide 0,9 bar < BP A1 < 1 bar entonces se finaliza la receta con el barril correctamente carbonatado, sino si BP A1 < 0,9 bar se pasa al paso 3.
3. Se inyectan 2 bares de CO2.
4. Se diluye el CO2 y si 0,9 bar < BP A1 < 1 bar se finaliza satisfactoriamente la receta, sino si BP A1 < 0,9 bar se pasa al paso 5.
5. Se inyecta 1 bar de CO2.
6. Se diluye el CO2 y si 0,9 bar < BP A1 < 1 bar se finaliza satisfactoriamente la receta, sino si BP A1 < 0,9 bar se repiten los pasos 5 y 6 indefinidamente.

En los pasos 2, 4 y 6 la condición BP A1 > 1 bar detiene la receta dado que no debería producirse si el sistema funciona adecuadamente. Se debe revisar el equipo.

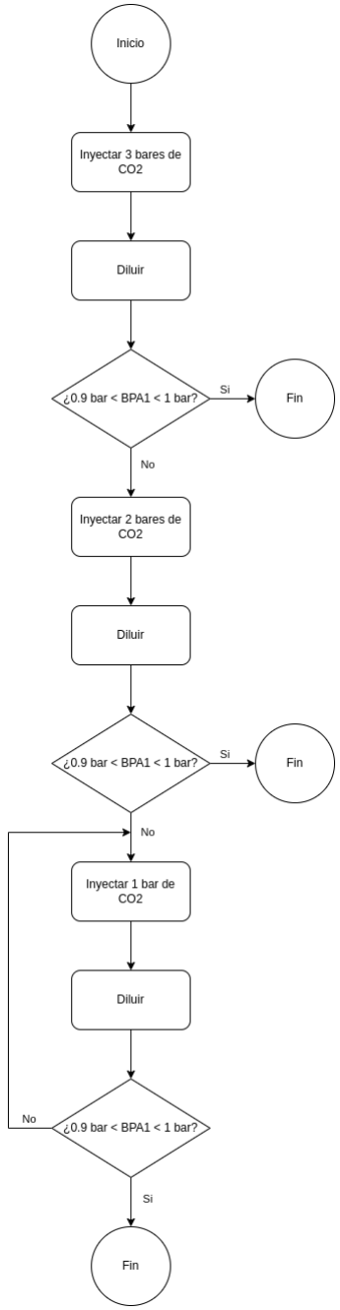
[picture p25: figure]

Figura 1.2: Diagrama de flujo de la receta de carbonatación.

### 1.3.2. Interacción del operador

La operación del sistema se basa en la ejecución de la receta de carbonatación, siguiendo el patrón de diseño de manufactura flexible ISA S88 [1].
El operador controla el estado de la receta a través de los siguientes comandos:

Start: inicia la receta.

Stop: detiene la receta.

Hold: pausa la receta.

Resume: reanuda la receta.

Reset: reinicia la receta.

Los comandos se encuentran ligados con los estados de la receta de acuerdo al diagrama de estados de la figura 1.3.

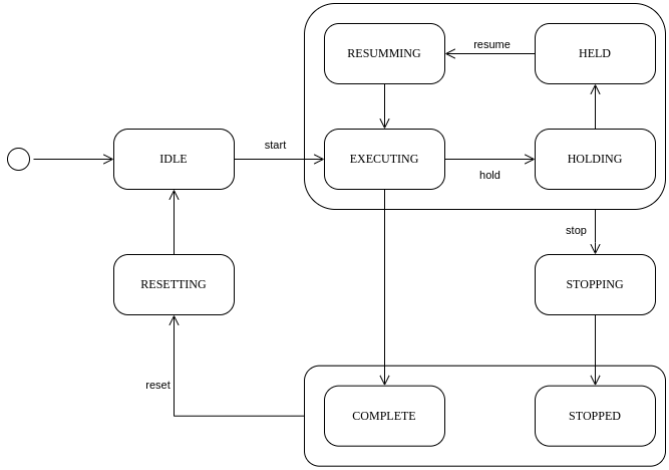
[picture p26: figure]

Figura 1.3: Diagrama de estados de la ejecución de la receta de carbonatación.

## 1.4. Arquitectura de control

El sistema de automatización se basa en una arquitectura de control típica como se muestra en la figura
1.4. Consta de un único controlador controlando el equipo físico, un HMI para operar y el soporte para una computadora de supervisión con la capacidad de monitorear el proceso, a través de una conexión serie o mediante un navegador web.

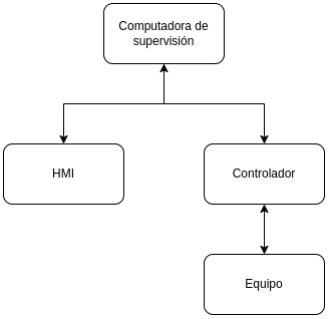
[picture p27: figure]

Figura 1.4: Arquitectura de control.

## 1.5. Análisis de sistemas similares en el mercado

En el mercado los carbonatadores que se venden son generalmente del tipo inline, para volúmenes altos de producción. El sistema a automatizar maneja volúmenes de producción bajos y por ende el carbonatador implementado opera directamente sobre los barriles. Sin embargo, se analizan tres sistemas de carbonatación comerciales para comparar las características de cada uno, en la tabla 1.1 se muestran los resultados de este análisis.
Los productos analizados se pueden encontrar en los siguientes enlaces:

ProCarb Mini (https://www.probrew.com/products/procarb-mini/)

Pentair Carbonation Control System (https://foodandbeverage.pentair.com/en/products/pentair-carbonation-control-system-carbo-controller-ccr)

Carboblend (https://www.alfalaval.com/products/process-solutions/brewery-solutions/blending-modules/carboblend/)

Característica | ProCarb Mini | Pentair Carbonation Control System | Carboblend
Automático | Si | Si | Si
HMI | Si | Si | Si
Compacto | Si | Si | Si
Medición directa de CO | Si | Si | Si
Comunicación abierta | Si | Si | Si

Tabla 1.1: Comparación de carbonatadores comerciales.

# Capítulo 2

# Introducción específica

## 2.1. Requisitos

En la tabla 2.1 se muestran los requisitos del sistema desarrollado.

Grupo | ID | Descripción
| 1.1 | Implementación de receta de carbonatación según ISA S88.
| 1.2 1.3 | Inyección de CO2 mediante válvula solenoide (QMB1). Disolución de CO2 mediante criba vibratoria accionada por motor eléctrico (MAA1). Control del proceso
1.4 | Monitoreo de presión (BPA1).
HMI | 2.1 | Comunicación con MCU.
| 2.2 | Indicación de estado de receta.
| 2.3 | Indicación de paso de receta.
| 2.4 | Indicación de alarmas.
| 2.5 | Indicación de presión BPA1.
| 2.6 | Botones de comando de receta: start, stop, hold, resume, reset.
| 3.1 3.2 | Conexión con MCU. Sirena Configuración de la alerta sonora.
Computadora de supervisión | 4.1 | Comunicación con MCU.
| 4.2 | Comandos de receta: start, stop, hold, resume, reset.
| 4.3 | Comando de reporte de presión BPA1.
| 4.4 | Comando de ayuda al operador.
Sistema de alarmas y enclavamientos | 5.1 | Alarma por sobrepresión cuando BP A1 > 4 bar.
| 5.2 | Detención del proceso por sobrepresión cuando BP A1 > 4 bar.
Servidor web | 6.1 | Comunicación WiFi con MCU.
| 6.2 | Implementación de servidor HTTP.
| 6.3 | Indicación de estado de receta mediante HTML.
| 6.4 | Indicación de paso de receta.
| 6.5 | Indicación de presión BPA1.
| 6.6 | Indicación de alarmas.

Tabla 2.1: Requisitos del sistema automático.

## 2.2. Casos de uso

En las tablas 2.2, 2.3 y 2.4 se presentan tres casos de uso del sistema representativos de su funcionalidad.

Caso de uso | Inicio de receta de carbonatación
Descripción | El operador inicia la receta para carbonatar un barril de cerveza.
Precondición | La receta debe estar en el estado Idle y el sistema no debe estar enclavado.
Flujo principal | 1. El operador selecciona Start en el HMI. 2. El sistema inicia la receta. 3. Se inyecta CO2 y se agita el barril según el algoritmo.
Flujo alternativo | Si se detecta BP A1 > 4 bar, se activa la alarma, se detiene el proceso y se notifica al operador.

Tabla 2.2: Caso de uso 1, inicio de la ejecución de la receta.

Caso de uso | Pausa y reanudación de receta
Descripción | El operador pausa temporalmente la receta en ejecución y luego la reanuda.
Precondición | La receta debe estar en el estado Executing.
Flujo principal | 1. El operador selecciona Hold en el HMI. 2. El sistema detiene la operación de los actuadores. 3. Posteriormente, selecciona Resume para continuar.
Flujo alternativo | Si la presión en el barril cambia mientras está pausado, se realiza una notificación visual en el HMI.

Tabla 2.3: Caso de uso 2, pausa y reanudación de receta

Caso de uso | Reporte de presión BPA1 a la computadora de supervisión.
Descripción | El operador se conecta a la computadora de supervisión comandando el reporte de la presión BPA1.
Precondición | La computadora de supervisión debe estar conectada a la interfaz UART.
Flujo principal | 1. El operador envía el comando ’r’ para inicial el reporte de la presión. 2. Se envía la presión BPA1 en un payload de JSON. 3. El operador envía el comando ’R’ para detener el reporte de la presión.
Flujo alternativo | -

Tabla 2.4: Caso de uso 3, reporte de presión BPA1 a la computadora de supervisión a través del terminal serie.

## 2.3. Descripción de módulos utilizados

En base a la arquitectura de control y los requisitos establecidos se decidió por utilizar los módulos que se describen a continuación.

### 2.3.1. Módulo del microcontrolador

Se utilizó como módulo microcontrolador la placa NUCLEO-F429ZI [5], equipada con un microcontrolador STM32F429ZI, figura 2.1.
Los principales puntos tenidos en cuenta para la adopción de esta placa son:

Rendimiento y recursos: El STM32F429ZI incluye un núcleo ARM Cortex-M4 de alto rendimiento con capacidad de punto flotante, ideal para realizar cálculos en tiempo real y ejecutar múltiples tareas si-multáneamente.

Periféricos integrados: La placa cuenta con una amplia gama de periféricos como UART, SPI, ADC y GPIO, que permiten una integración eficiente con los sensores y actuadores del sistema.

Compatibilidad con herramientas de desarrollo: La placa es compatible con Mbed OS y herramientas como STM32CubeIDE, lo que facilita el desarrollo del software.

Documentación y soporte: La disponibilidad de documentación detallada simplifica el proceso de implementación y resolución de problemas.

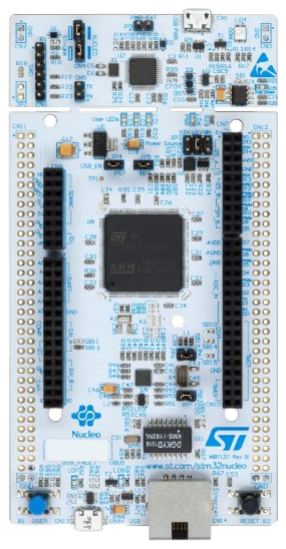
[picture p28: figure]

Figura 2.1: NUCLEO-F429ZI.

### 2.3.2. Módulo del display táctil

Para la implementación del HMI se utilizó el módulo display [4] con pantalla LCD TFT de 2.4’ y drivers de hardware ILI9341 y XPT2046 que se muestra en la figura 2.2.
El comando gráfico del LCD se realiza con el hardware ILI9341 a través de una comunicación SPI y el comando de la interacción táctil con el hardware XPT2046 también a través de una comunicación SPI.

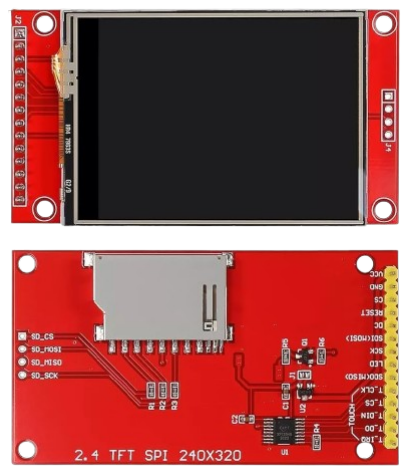
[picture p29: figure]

Figura 2.2: Modulo display táctil.

### 2.3.3. Módulo Wi-Fi

Para la implementación de la comunicación con la computadora de supervisión a través de un navegador web se utiliza el módulo Wi-Fi ESP01 [2] de la figura 2.3.
Este módulo se comunica con el microcontrolador a través de una interfaz UART y la configuración del mismo se realiza a través de comandos AT.

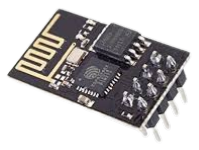
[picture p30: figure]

Figura 2.3: Modulo ESP01.

### 2.3.4. Buzzer

Para las indicaciones auditivas se utiliza el buzzer pasivo KY-006 que se muestra en la figura 2.4. El dispositivo se activa enviando una señal PWM al terminal de entrada.

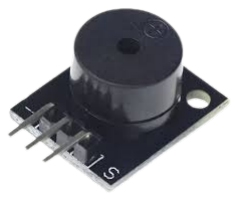
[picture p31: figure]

Figura 2.4: Buzzer

### 2.3.5. Módulo de alimentación

Para la alimentación de los módulos de display, Wi-Fi y el buzzer se utiliza el módulo MB102 que se muestra en la figura 2.5. El dispositivo genera 3,3 V al conectar el USB de entrada a 5 V .

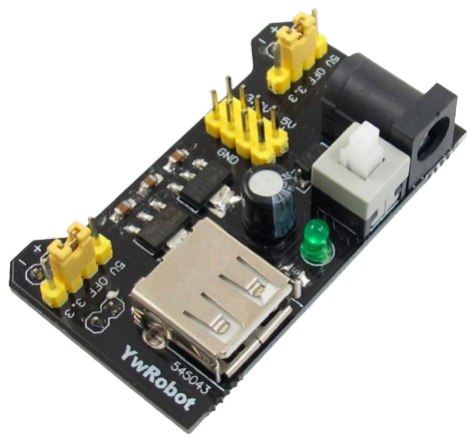
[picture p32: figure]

Figura 2.5: Módulo de alimentación MB102.

# Capítulo 3

# Diseño e implementación

## 3.1. Hardware

### 3.1.1. Diagrama en bloques

En la figura 3.1 se muestra un diagrama en bloques del hardware del sistema de automatización desarrollado.

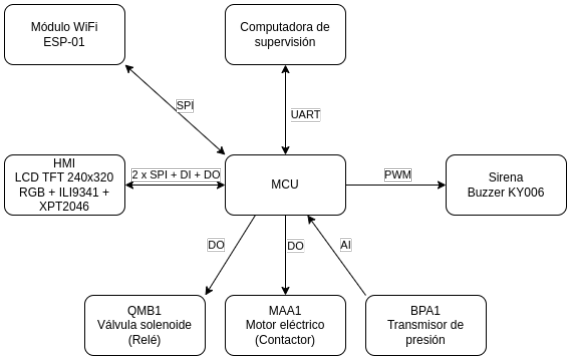
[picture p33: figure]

Figura 3.1: Diagrama en bloque del sistema

### 3.1.2. Lista de señales

En la tabla 3.1 se listan las señales del sistema, indicando la conexión de los puertos de la placa NUCLEO-F429ZI a los módulos de hardware, los relé de accionamiento del motor MAA1 y la válvula QMB1 y la entrada analógica del sensor de presión BPA1.

Pin del módulo de hardware | Pin de la placa Nucleo-F429ZI
ILI9341 | MISO | PB4 | SPI1 MISO
| SCKL | PB3 | SPI1 SCK
| MOSI | PB5 | SPI1 MOSI
| CS | PA4 | SPI1 CS
| DCX | PC7 | DO
| RESX | PA15 | DO
XPT2046 | MISO | PC2 | SPI2 MISO
| SCKL | PB13 | SPI2 SCK
| MOSI | PB15 | SPI2 MOSI
| CS | PB12 | SPI2 CS
| PENIRQ | PC6 | DI
Siren | Signal | PA3 | PWM2/4
ESP01 | Tx | PD5
| Rx | PD6
| Enable | PD7
BPA1 | Signal | PC0 | AI
MAA1 | Relay | PB0 | DO
QMB1 | Relay | PB7 | DO

Tabla 3.1: Lista de señales del sistema.

### 3.1.3. Pantalla del HMI

La pantalla del HMI implementada se muestra en la figura 3.2. A través de los botones táctiles se controla la ejecución de la receta y con los indicadores se monitorea el estado.

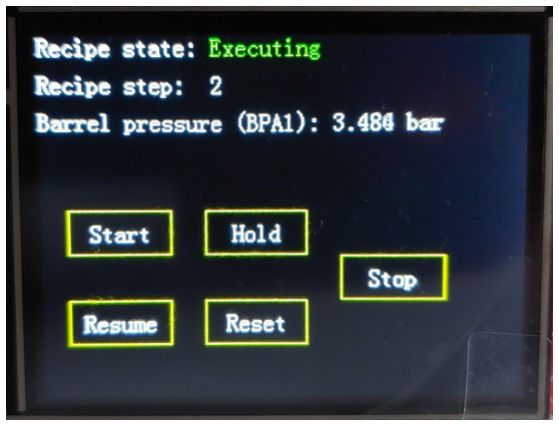
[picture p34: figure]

Figura 3.2: Pantalla del HMI.

## 3.2. Firmware

### 3.2.1. Repositorio

Todo el código del proyecto se encuentra en el repositorio git en [7].

### 3.2.2. Tecnología

El firmware del proyecto se desarrolla en el sistema operativo Mbed en lenguaje C++. Como compilador se utilizó la toolchain ARM-GNU.

### 3.2.3. Estructura del repositorio

El repositorio git se divide en las siguientes carpetas y archivos:

doc: Documentación del proyecto.

include: Archivos de cabecera de c++.

lib: Bibliotecas externas. Contiene la librería mbed-os como submodulo de git.

src: Archivos fuente de c++.

test: Archivos de soporte para pruebas de software.

CMakeLists.txt: Archivo de compilación de cmake.

Doxyfile: Archivo de configuración de la documentación Doxygen.

mbed app.json: Archivo de configuración de mbed.

mbed-os.lib: Archivo de configuración de mbed.

### 3.2.4. Documentación

El código fuente se encuentra documentado con Doxygen, ver instrucciones en [7] para su generación. En el presente documento se muestran detalles de alto nivel de las clases, recurrir a esta documentación en caso de requerir mayor detalle.

### 3.2.5. Compilación

El proyecto se compiló utilizando la toolchain de código libre ARM-GNU, ver instrucciones en [7].

### 3.2.6. Arquitectura

En la figura 3.3 se muestra el diagrama UML del sistema. La clase contenedora es BeerCarbonationSystem. Los módulos se comunican entre sí adquiriendo referencias de los objetos necesarios.


Figura 3.3: Diagrama UML del sistema.

### 3.2.7. Clase BeerCarbonationSystem

La clase BeerCarbonationSystem implementa la lógica de una célula de proceso para la carbonatación de cerveza, siguiendo el patrón de diseño ISA S88. Esta clase gestiona la interfaz de usuario, ejecuta las recetas de carbonatación y controla los equipos relacionados con el proceso.

### 3.2.8. Clase CarbonationRecipe

La clase CarbonationRecipe implementa la receta de carbonatación de acuerdo al patrón ISA S88, permitiendo el control del estado de acuerdo a la máquina de estados de la figura 3.4.
Implementa el enclavamiento de protección en caso de sobrepresión BP A1 > 4 bar, deteniendo el proceso y evitando su reanudación hasta que esta condición desaparezca.


Figura 3.4: Diagrama de estados de la clase CarbonationRecipe.

Dentro del estado EXECUTING se encuentra la máquina de estados de la figura 3.5 que implementa la receta por pasos:


Figura 3.5: Diagrama de estados de los pasos de la receta de carbonatación.

### 3.2.9. Clase Carbonator

Implementa el modelo del equipo carbonatador, corresponde a una unit del modelo ISA S88. Se encarga de propagar las señales entre los equipos de la unidad y el gestor de la receta, ofreciendo una interfaz para la ejecución de sus fases.

### 3.2.10. Clase CO2Injector

Implementa la fase de inyección de CO2 al barril de la figura 3.6 permitiendo configurar la presión deseada por parámetro.


Figura 3.6: Diagrama de flujo de la fase de inyección de CO2.

Internamente contiene una máquina de estados como la de la figura 3.4 que indica el estado del equipo siguiendo el estado de la receta y una máquina de estados por pasos para implementar la lógica de la fase en el estado EXECUTING.

### 3.2.11. Clase CO2Dissolver

Implementa la fase de disolución de CO2 al barril de la figura 3.7.


Figura 3.7: Diagrama de flujo de la fase de disolución de CO2.

Internamente contiene una máquina de estados como la de la figura 3.4 que indica el estado del equipo siguiendo el estado de la receta y una máquina de estados por pasos para implementar la lógica de la fase en el estado EXECUTING.

### 3.2.12. Clase PressureTransmitter

La clase PressureTransmitter está diseñada para leer y convertir una señal analógica proveniente de un transmisor de presión en una magnitud de presión. Utiliza un pin de entrada analógica para leer el valor de la señal y luego escala este valor para obtener la presión en unidades de presión.
El tranmisor tiene un rango de 0 a 5 bar y produce señales de tensión de 0 a 3,3 V .

Componentes principales:

pressure signal: Es un objeto de tipo AnalogIn, que representa el pin analógico al que está conectada la señal del transmisor de presión. Se utiliza para leer el valor de la señal analógica.

### 3.2.13. Clase OnOffMotor

La clase OnOffMotor controla un motor que puede ser encendido o apagado con un control binario. La clase maneja los estados del motor y proporciona un control suave, gestionando los tiempos de respuesta del motor cuando cambia entre los estados de encendido y apagado.
La máquina de estados implementada por esta clase se muestra en la figura 3.8.


Figura 3.8: Diagrama de estados de la clase OnOffMotor.

Componentes principales:

on actuating signal: objeto que controla el pin de salida digital conectado al motor o válvula solenoide. El valor de este pin determina si el motor está encendido (true) o apagado (false).

response time: El tiempo de respuesta del motor, que define cuánto tiempo tarda en cambiar de estado de encendido o apagado. Este parámetro es útil para gestionar transiciones suaves entre los estados.

### 3.2.14. Clase SolenoidValve

El propósito de la clase SolenoidValve es proporcionar un control sencillo y eficiente de una válvula solenoide, permitiendo su activación o desactivación con una señal binaria. La clase asegura que las transiciones entre los estados de la válvula (abierta y cerrada) se realicen de manera controlada, teniendo en cuenta el tiempo de respuesta de la válvula.
La máquina de estados implementada por esta clase se muestra en la figura 3.9.


Figura 3.9: Diagrama de estados de la clase SolenoidValve.

Componentes principales:

on actuating signal: objeto que controla el pin de salida digital conectado al motor o válvula solenoide. El valor de este pin determina si el motor está encendido (true) o apagado (false).

response time: El tiempo de respuesta de la válvula solenoide, que define cuánto tiempo tarda en cambiar de estado de encendido o apagado. Este parámetro es útil para gestionar transiciones suaves entre los estados.

### 3.2.15. Clase AlarmSystem

La clase AlarmSystem implementa el sistema de alarmas del proceso de carbonatación. Su principal función es monitorear las condiciones críticas definidas en el proceso y activar alarmas en caso de detectar situaciones anómalas.
El sistema incluye un registro de alarmas que se evalúan periódicamente, activando una sirena en caso de que alguna alarma esté activa.

Alarmas implementadas: Sobrepresión del barril: Se activa cuando la presión del sensor BPA1 excede los 4 bar.

Componentes principales:

Registro de alarmas: Cada alarma está definida por un mensaje descriptivo, una condición de activación (trigger) y un estado actual (ACTIVA o INACTIVA).

Siren: Buzzer que se activa en caso de alarmas activas.

### 3.2.16. Clase Siren

La clase Siren controla una sirena mediante una señal PWM (Pulse Width Modulation). Permite activar o desactivar la sirena y configurar la frecuencia de su tono. Es utilizada como un mecanismo de notificación acústica en el sistema.

Componentes principales:

on actuating signal: Señal PWM utilizada para controlar la sirena.

Frecuencia del tono: Configurable dinámicamente para ajustar el sonido emitido por la sirena.

### 3.2.17. Clase HMI

La clase HMI gestiona la interfaz de usuario del sistema de carbonatación, controlando la pantalla LCD y la interacción táctil para monitorear y controlar el proceso de carbonatación.

Componentes principales:

LCD driver ILI9341: Se utiliza para mostrar información al usuario, como el estado de la receta, la presión del barril y los pasos del proceso de carbonatación.

Driver táctil XPT2046: Permite la interacción táctil del usuario con la interfaz, detectando toques y gestos en la pantalla.

### 3.2.18. Clase ILI9341

La clase ILI9341 es una implementación para controlar una pantalla LCD basada en el controlador ILI9341. Utiliza una comunicación SPI para interactuar con el hardware y proporciona métodos para dibujar píxeles, líneas, rectángulos, imágenes y llenar la pantalla con un color específico. También incluye funciones de inicialización y control de la pantalla.

Componentes principales:

SPI: Interfaz de comunicación para enviar y recibir datos.

CS (Chip Select): Pin para seleccionar el dispositivo ILI9341.

DCX (Data/Command): Pin para indicar si se están enviando datos o comandos.

RESX (Reset): Pin para realizar un reset hardware en la pantalla.

### 3.2.19. Clase XPT2046

La clase XPT2046 proporciona la interfaz para interactuar con el controlador táctil de la pantalla, que utiliza el chip XPT2046. Esta clase maneja la comunicación SPI y las interrupciones para detectar eventos táctiles, como presionar y soltar.

Componentes principales:

SPI: Interfaz de comunicación para enviar y recibir datos.

CS (Chip Select): Pin para seleccionar el dispositivo ILI9341.

penirq (Pin de Interrupción): Pin de interrupción que detecta eventos táctiles, como cuando la pantalla es tocada o liberada. Utiliza una interrupción externa para activar funciones de callback definidas por el usuario, lo que permite responder a los eventos de toque en tiempo real.

Callback para eventos táctiles: Funciones que se ejecutan cuando se detecta que la pantalla ha sido tocada (onTouchPressed) o cuando el toque ha sido liberado (onTouchReleased). Estas funciones son proporciona-das por el usuario al crear el objeto de la clase XPT2046.

### 3.2.20. Clase WebServer

La clase WebServer gestiona la comunicación entre el sistema de carbonatación y un servidor web, permitiendo la visualización remota del estado del proceso de carbonatación a través de una interfaz web. Utiliza un módulo ESP01 para la conexión Wi-Fi y la transmisión de información.

Componentes principales:

esp01: Objeto que representa el módulo ESP01, responsable de la conexión Wi-Fi y la gestión de solicitudes HTTP.

### 3.2.21. Clase ESP01

La clase ESP01 gestiona la comunicación con el módulo Wi-Fi ESP01, permitiendo la conexión a una red Wi-Fi, la recepción de solicitudes HTTP y el envío de respuestas. Utiliza comandos AT para interactuar con el ESP01 y establece una conexión en modo estación, permitiendo la interacción con un servidor web.

Componentes principales:

uart: Interfaz UART para la comunicación serial con el módulo ESP01, configurada a 115200 baudios.

enable: Salida digital para habilitar o deshabilitar el módulo ESP01.

### 3.2.22. Clase SupervisoryComputer

La clase SupervisoryComputer permite conectar un operador al sistema de carbonatación de cerveza, faci-litando la supervisión y control remoto del proceso. A través de una interfaz UART, el operador puede enviar comandos para iniciar, detener, pausar, reanudar o restablecer el proceso de carbonatación. Además, esta clase permite obtener reportes en tiempo real sobre el estado del proceso, como la presión de la carbonatación, sin ser directamente responsable de ejecutar el proceso de carbonatación en sí.

Componentes principales:

uart (Interfaz UART):La comunicación entre el operador y el sistema se realiza a través de una interfaz UART a 9600 baudios. El operador envía comandos al sistema, y el sistema responde con información o reportes, lo que permite al operador supervisar el estado del proceso. ReportingState:Esta enumeración gestiona el estado de los reportes. Los reportes pueden estar en estado REPORTING”(enviando datos) o

ÏDLE”(sin reportar). El estado de reporte permite al operador recibir información periódica sobre el proceso.

# Capítulo 4

# Ensayos y resultados

## 4.1. Pruebas funcionales del hardware

Las pruebas funcionales del hardware se realizaron por módulos.

### 4.1.1. Módulo Wi-Fi ESP01

Se conectó el módulo a la placa y en paralelo un analizador de protocolos para verificar el correcto envío de comandos y la recepción de respuestas.

### 4.1.2. Módulo HMI

Se conectó el módulo a la placa y se realizó la calibración del display mediante la graficación de puntos. Adicoinalmente se conectó un analizador de protocolos en los pines de comunicación ambos SPI para verificar el correcto envío de comandos y la recepción de respuestas.

### 4.1.3. Módulo buzzer

Se conectó el buzzer al terminal de masa y se le envío una señal PWM con la placa nucleo verificando el correcto funcionamiento.

### 4.1.4. Transmisor de presión

El transmisor de presión se simuló mediante un potenciometro de 50 kΩ. Se conectó el mismo a los 3,3 V generados por la placa y se verificó que el valor medido por el objeto AnalogIn sea consistente con las mediciones realizadas con multímetro.

### 4.1.5. Módulo de alimentación

Se conectó el módulo de alimentación al protoboard y a la fuente de 5 V . Se verificó mediante una medición de voltímetro que la tensión generada era de 3,3 V .

### 4.1.6. Motor MAA1 y válvula solenoide QMB1

Para demostrar el correcto funcionamiento de las salidas digitales correspondientes al motor MAA1 y QMB1 se conectaron sus salidas a los LEDs 1 y 2 de la placa NUCLEO.

### 4.1.7. Pruebas funcionales del firmware

Las pruebas funcionales del firmware se realizaron en conjunto con las distintas pruebas para los módulos de hardware.
La lógica de la receta se verificó mediante el uso del debugger.

### 4.1.8. Pruebas de integracion

Las pruebas de integración realizadas se encuentran en formato de video en [6]. Se verificó:

Disposición del hardware.

Lógica de la receta y respuesta a comandos.

Comandos mediante la computadora de supervisión por terminal serie.

Monitoreo mediante el servidor web.

Alarmas y enclavamientos.

### 4.1.9. Cumplimiento de requisitos

En la tabla 4.1 se presenta la evaluación del cumplimiento de los requisitos iniciales de la tabla 2.1. Se evaluó a el estado actual de cada uno indicando en verde aquellos que ya fueron cumplidos y en rojo los requerimientos no cumplidos.

Grupo | ID | Descripción
| 1.1 | Implementación de receta de carbonatación según ISA S88
| 1.2 1.3 | Inyección de CO2 mediante válvula solenoide (QMB1) Disolución de CO2 mediante criba vibratoria accionada por motor eléctrico (MAA1) Control del proceso
1.4 | Monitoreo de presión (BPA1)
HMI | 2.1 | Comunicación con MCU
| 2.2 | Indicación de estado de receta
| 2.3 | Indicación de paso de receta
| 2.4 | Indicación de alarmas
| 2.5 | Indicación de presión BPA1
| 2.6 | Botones de comando de receta: start, stop, hold, resume, reset
| 3.1 3.2 | Conexión con MCU Sirena Configuración de la alerta sonora
Computadora de supervisión | 4.1 | Comunicación con MCU
| 4.2 | Comandos de receta: start, stop, hold, resume, reset
| 4.3 | Comando de reporte de presión BPA1
| 4.4 | Comando de ayuda al operador
Sistema de alarmas y enclavamientos | 5.1 | Alarma por sobrepresión cuando BPA1 >4 bar
| 5.2 | Detención del proceso por sobrepresión cuando BPA1 >4 bar
Servidor web | 6.1 | Comunicación WiFi con MCU
| 6.2 | Implementación de servidor HTTP
| 6.3 | Indicación de estado de receta mediante HTML
| 6.4 | Indicación de paso de receta
| 6.5 | Indicación de presión BPA1
| 6.6 | Indicación de alarmas

Tabla 4.1: Estado de los requisitos.

## 4.2. Documentación del desarrollo realizado

Elemento | Referencia
Presentación del proyecto | Capítulo 1
Listado de requisitos | Tabla 2.1
Casos de uso del proyecto | Tablas 2.2 a 2.3
Diagrama en bloques del sistema | Figura 3.1
Lista de señales | Tabla 3.1
Implementación del hardware | Sección 3.1
Módulos de software | Sección 3.2
Repositorio | \cite{REPO}
Cumplimiento de requisitos | Tabla 4.1
Conclusiones finales | Capítulo 5

Tabla 4.2: Elementos del sumario del sistema automático para el sistema de carbonatación de cerveza.

# Capítulo 5

# Conclusiones

## 5.1. Resultados obtenidos

El sistema desarrollado en base al patrón de diseño de ISA S88 resulta mantenible, escalable y extensible. Por otro lado, implementar el proyecto en mbed aceleró los tiempos de desarrollo pero significó una perdida de dominio en cuanto a conocimiento interno del sistema operativo.
Teniendo en cuenta que el soporte para mbed finaliza en 2026 es conveniente migrar el código para utilizar solo la libreria STM32CubeF4.

## 5.2. Próximos pasos

Migrar el código desde mbed a la librería STM32CubeF4.

Crear un worflow con la toolchain ARM-GNU de forma de independizarse de los IDE para automatizar tareas y lograr control total del proceso.

Crear y automatizar pruebas unitarias y de integración mediante un esquema xUnit.

Refactorizar la clase WebServer para gestionar mejor los tiempos de espera y la latencia de las peticiones.

# Bibliografía

[1] Brandl, Dennis. Design Patterns for Flexible Manufacturing. (ISA, 2007).
[2] Shenzhen | Anxinke | Technology | CO. ESP-01 WiFi Module. (2015). Disponible en https://www.
microchip.ua/wireless/esp01.pdf al [12/12/2024].
[3] International Electrotechnical Commission. IEC 81346-2:2019: Industrial systems, installations and equipment and industrial products — Structuring principles and reference designations — Part 2: Classifica-tion of objects and codes for classes. (IEC, 2019).
[4] LCD wiki. 2.8inch SPI Module ILI9341 SKU:MSP2807. Disponible en http://www.lcdwiki.com/2.8inch_SPI_Module_ILI9341_SKU:MSP2807 (http://www.lcdwiki.com/2.8inch_SPI_Module_ILI9341_SKU:MSP2807) al [12/12/2024].
[5] ST Microelectronics. NUCLEO-F429ZI. Disponible en https://www.st.com/en/evaluation-tools/nucleo-f429zi.html (https://www.st.com/en/evaluation-tools/nucleo-f429zi.html) al [12/12/2024].
[6] Bailo, Hernan L. ´ . Pruebas de integración del sistema Beer Carbonation System. Disponible en https://drive.google.com/drive/folders/1NrQh9VOOGA5issQOtzWXVuDIw9n37sIr?usp=sharing al [12/12/2024].
[7] Bailo, | Hernan | L. ´ | . | Beer Carbonation | System. | Disponible | en | https://github.com/hbailo/
beer-carbonation-system (https://github.com/hbailo/beer-carbonation-system) al [12/12/2024].

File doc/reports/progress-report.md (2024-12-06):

# Sistema de carbonatación de cerveza

**Informe de avance**

**Autor:** Hernán Leandro Bailo

**Padrón:** 97841

**Fecha:** 2° cuatrimeste del 2024

## Cumplimiento de los requerimientos

En base a los requerimientos planteados en la definición del proyecto, archivo `requirements-and-use-cases.md` de la carpeta `doc`, se evalúa el estado actual de cada uno indicando en verde aquellos que ya fueron cumplidos, en amarillo los que aún no fueron cumplidos pero se proyecta que será posible hacerlo, y en rojo los requerimientos que no serán cumplidos. El estado de los requerimientos se muestra en la tabla 1.

<picture>
    Requirements progress table
</picture>

**Tabla 1: Estado de los requerimientos.**

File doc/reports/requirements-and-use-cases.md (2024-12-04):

# Sistema de carbonatación de cerveza

**Autor:** Hernán Leandro Bailo

**Padrón:** 97841

**Fecha:** 2° cuatrimeste del 2024

## 1 Selección de proyecto

### 1.1 Análisis de alternativas

Inicialmente se analizaron dos posibles alternativas de proyecto:

* Sistema de riego doméstico inteligente.

* Sistema de carbonatación de cerveza en barriles.

Las alternativas se evaluaron en base al puntaje otorgado en las siguientes categorías:

1) Utilidad económica: satisfacción del consumidor del sistema.
3) Indisponibilidad de alternativas: falta de sistemas similares en el mercado.
4) Tiempo de desarrollo: extensión del diseño y la implementación.
5) Research & Development: creación de nuevo know how.

En la tabla 1 se muestran los puntajes otorgados a ambos proyectos en estas categorías y el resultado de la suma pesada.

<table class="tg" style="undefined;table-layout: fixed; width: 1239px"><colgroup>
<col style="width: 259px">
<col style="width: 80px">
<col style="width: 180px">
<col style="width: 180px">
<col style="width: 180px">
<col style="width: 180px">
<col style="width: 180px">
</colgroup>
<thead>
  <tr>
    <th class="tg-qbk9" colspan="2">Proyecto</th>
    <th class="tg-qbk9">Utilidad económica<br><span style="font-weight:bold">(Peso 7)</span></th>
    <th class="tg-ncfi">Indisponibilidad de<br>alternativas <br>(Peso 10)</th>
    <th class="tg-ncfi">Tiempo de<br>desarrollo<br>(Peso 5)</th>
    <th class="tg-ncfi">Research &amp; Development<br>(Peso 9)</th>
    <th class="tg-ncfi">Suma de puntajes<br>pesados</th>
  </tr></thead>
<tbody>
  <tr>
    <td class="tg-lboi" rowspan="2">Sistema de riego doméstico inteligente</td>
    <td class="tg-c3ow">Puntaje<br>categoría</td>
    <td class="tg-9wq8">2</td>
    <td class="tg-nrix">4</td>
    <td class="tg-nrix">6</td>
    <td class="tg-nrix">5</td>
    <td class="tg-nrix">-</td>
  </tr>
  <tr>
    <td class="tg-c3ow">Puntaje<br>pesado</td>
    <td class="tg-9wq8">14</td>
    <td class="tg-nrix">40</td>
    <td class="tg-nrix">30</td>
    <td class="tg-nrix">45</td>
    <td class="tg-nrix">129</td>
  </tr>
  <tr>
    <td class="tg-cly1" rowspan="2">Sistema de carbonatación de cerveza</td>
    <td class="tg-baqh">Puntaje<br>categoría</td>
    <td class="tg-nrix">9</td>
    <td class="tg-nrix">10</td>
    <td class="tg-nrix">8</td>
    <td class="tg-nrix">10</td>
    <td class="tg-nrix">-</td>
  </tr>
  <tr>
    <td class="tg-baqh">Puntaje<br>pesado</td>
    <td class="tg-nrix">63</td>
    <td class="tg-nrix">100</td>
    <td class="tg-nrix">40</td>
    <td class="tg-nrix">90</td>
    <td class="tg-nrix">293</td>
  </tr>
</tbody></table>

**Tabla 1: Comparación de las alternativas de proyecto basada en el puntaje de las categorías seleccionadas.**

El proyecto de mayor puntaje pesado y por ende seleccionado para su desarrollo es el Sistema de Carbonatación de Cerveza. A continuación se realiza un análisis de los puntajes asignados a cada categoría.

#### Utilidad económica
Al sistema de carbonatación de cerveza en barriles se le asigna un puntaje de 9 dado que el sistema va a ser utilizado por el dueño del equipo físico que actualmente realiza el procedimiento de forma manual. La automatización del sistema le genera gran utilidad dado que va a poder utilizar el tiempo en otras tareas de la planta a la vez que incrementa los volúmenes de producción y mejora la repetibilidad del proceso.

Al sistema de riego doméstico inteligente se le asigna un puntaje de 2 dado que es un proyecto personal para el riego en mi domicilio y no me es relevante actualmente.

#### Indisponibilidad de alternativas
Al sistema de carbonatación se le asigna un puntaje de 10 dado que el equipo físico ya está opeartivo y el desarrollo del sistema tiene que ser a medida de los instrumentos ya adquiridos.

Al sistema de riego se le asigna un puntaje de 4 dado que existe una amplia gama de productos comerciales de riego.

#### Tiempo de desarrollo
Al sistema de carbonatación se le asigna un puntaje de 8 dado que el sistema debe implementar una receta de manufactura compleja, junto con la interfaz con el operador.

Al sistema de riego se le asigna un puntaje de 6 dado que la lógica del riego a implementar es más directa que para el carbonatador.

#### Research & Development
Al sistema de carbonatación se le asigna un puntaje de 10, frente al 5 del sistema de riego, ya que al ser un equipo a medida y una aplicación menos común se requiere de investigar y desarrollar más otorgando un know how superior.

### 1.2 Objetivo del proyecto seleccionado
Implementar la automatización del sistema de carbonatación de cerveza en barriles que se muestra esquemáticamente en el P&ID de la figura 1.

<picture>
    <source media="(prefers-color-scheme: dark)" srcset="architecture/process-and-instrumentation-diagram-dark.png">
    <source media="(prefers-color-scheme: light)" srcset="architecture/process-and-instrumentation-diagram-light.png"> 
    Shows the recipe state diagram.
</picture>

**Figura 1: P&ID del sistema de carbonatación de cerveza en barriles**

## 2 - Elicitación de requisitos y casos de uso

### 2.1 Productos similares en el mercado
En el mercado los carbonatadores que se venden son generalmente del tipo inline, para volúmenes altos de producción. El sistema a automatizar maneja volúmenes de producción bajos y por ende el carbonatador implementado opera directamente sobre los barriles. Sin embargo, se analizan tres sistemas de carbonatación comerciales para comparar las características de cada uno, en la tabla 2 se muestran los resultados de este análisis.

Los productos analizados se pueden encontrar en los siguientes enlaces:

* [ProCarb™ Mini](https://www.probrew.com/products/procarb-mini/)
* [Pentair Carbonation Control System](https://foodandbeverage.pentair.com/en/products/pentair-carbonation-control-system-carbo-controller-ccr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)
* [Carboblend](https://www.alfalaval.com/products/process-solutions/brewery-solutions/blending-modules/carboblend/)

<table><thead>
  <tr>
    <th>Característica</th>
    <th>ProCarb™ Mini</th>
    <th>Pentair Carbonation<br>Control System</th>
    <th>Carboblend</th>
  </tr></thead>
<tbody>
  <tr>
    <td>Automático</td>
    <td>Si</td>
    <td>Si</td>
    <td>Si</td>
  </tr>
  <tr>
    <td>HMI</td>
    <td>Si</td>
    <td>Si</td>
    <td>Si</td>
  </tr>
  <tr>
    <td>Compacto</td>
    <td>Si</td>
    <td>Si </td>
    <td>Si</td>
  </tr>
  <tr>
    <td>Medición directa<br>de CO₂</td>
    <td>Si</td>
    <td>Si</td>
    <td>Si</td>
  </tr>
  <tr>
    <td>Comunicación<br>abierta</td>
    <td>Si</td>
    <td>Si</td>
    <td>Si</td>
  </tr>
</tbody>
</table>

**Tabla 2: Comparación de carbonatadores comerciales.**

### 2.2 Requerimientos
En la tabla 3 se muestran los requerimientos de la automatización del sistema de carbonatación de cerveza.

<table><thead>
  <tr>
    <th>Grupo</th>
    <th>ID</th>
    <th>Descripción</th>
  </tr></thead>
<tbody>
  <tr>
    <td rowspan="4">Control del proceso</td>
    <td>1.1</td>
    <td>Implementación de receta de carbonatación según ISA S88</td>
  </tr>
  <tr>
    <td>1.2</td>
    <td>Inyección de CO2 mediante válvula solenoide (QMB1)</td>
  </tr>
  <tr>
    <td>1.3</td>
    <td>Disolución de CO2 mediante criba vibratoria accionada por motor eléctrico (MAA1)</td>
  </tr>
  <tr>
    <td>1.4</td>
    <td>Monitoreo de presión (BPA1)</td>
  </tr>
  <tr>
    <td rowspan="6">HMI</td>
    <td>2.1</td>
    <td>Comunicación con MCU</td>
  </tr>
  <tr>
    <td>2.2</td>
    <td>Indicación de estado de receta</td>
  </tr>
  <tr>
    <td>2.3</td>
    <td>Indicación de paso de receta</td>
  </tr>
  <tr>
    <td>2.4</td>
    <td>Indicación de alarmas</td>
  </tr>
  <tr>
    <td>2.5</td>
    <td>Indicación de presión BPA1</td>
  </tr>
  <tr>
    <td>2.6</td>
    <td>Botones de comando de receta: start, stop, hold, resume, reset</td>
  </tr>
  <tr>
    <td rowspan="2">Sirena</td>
    <td>3.1</td>
    <td>Conexión con MCU</td>
  </tr>
  <tr>
    <td>3.2</td>
    <td>Configuración de la alerta sonora</td>
  </tr>
  <tr>
    <td rowspan="4">Computadora de<br>supervisión</td>
    <td>4.1</td>
    <td>Comunicación con MCU</td>
  </tr>
  <tr>
    <td>4.2</td>
    <td>Comandos de receta: start, stop, hold, resume, reset</td>
  </tr>
  <tr>
    <td>4.3</td>
    <td>Comando de reporte de presión BPA1</td>
  </tr>
  <tr>
    <td>4.4</td>
    <td>Comando de ayuda al operador</td>
  </tr>
  <tr>
    <td rowspan="2">Sistema de alarmas<br>y enclavamientos</td>
    <td>5.1</td>
    <td>Alarma por sobrepresión cuando BPA1 &gt; 4 bar</td>
  </tr>
  <tr>
    <td>5.2</td>
    <td>Detención del proceso por sobrepresión cuando BPA1 &gt; 4 bar</td>
  </tr>
  <tr>
    <td rowspan="6">Servidor web</td>
    <td>6.1</td>
    <td>Comunicación WiFi con MCU</td>
  </tr>
  <tr>
    <td>6.2</td>
    <td>Implementación de servidor HTTP</td>
  </tr>
  <tr>
    <td>6.3</td>
    <td>Indicación de estado de receta mediante HTML</td>
  </tr>
  <tr>
    <td>6.4</td>
    <td>Indicación de paso de receta</td>
  </tr>
  <tr>
    <td>6.5</td>
    <td>Indicación de presión BPA1</td>
  </tr>
  <tr>
    <td>6.6</td>
    <td>Indicación de alarmas</td>
  </tr>
</tbody></table>

**Tabla 3: requerimientos del sistema de carbonatación de cerveza.**

En la figura 2 se muestra un diagrama de bloques del sistema diseñado.

<picture>
    <source media="(prefers-color-scheme: dark)" srcset="design/system-block-diagram-dark.png">
    <source media="(prefers-color-scheme: light)" srcset="design/system-block-diagram-light.png"> 
    Shows the recipe state diagram.
</picture>

**Figura 2: Diagrama de bloques del sistema.**

### 2.3 Casos de uso

En la tabla 4 se describen tres casos de uso del sistema.

<table><thead>
  <tr>
    <th>Caso de Uso</th>
    <th>Descripción</th>
    <th>Precondición</th>
    <th>Flujo Principal</th>
    <th>Flujo Alternativo</th>
  </tr></thead>
<tbody>
  <tr>
    <td>Inicio de Receta de Carbonatación</td>
    <td>El operador inicia la receta para carbonatar un barril de cerveza.</td>
    <td>La receta debe estar en el estado Idle<br>y el sistema no debe estar enclavado.</td>
    <td>1. El operador selecciona Start en el HMI.<br>2. El sistema inicia la receta.<br>3. Se inyecta CO2 y se agita el barril según el algoritmo.                </td>
    <td>         Si el sensor BPA1 detecta presión &gt; 4 bar, se activa la alarma, se detiene el proceso y se notifica al operador.       </td>
  </tr>
  <tr>
    <td>Pausa y Reanudación del Proceso</td>
    <td>El operador pausa temporalmente la receta en ejecución y luego la reanuda.</td>
    <td>La receta debe estar en el estado Executing.</td>
    <td>1. El operador selecciona Hold en el HMI.<br>2. El sistema detiene la operación de los actuadores.<br>3. Posteriormente, selecciona Resume para continuar.                </td>
    <td>         Si la presión en el barril cambia mientras está pausado, se realiza una notificación visual en el HMI.       </td>
  </tr>
  <tr>
    <td>Reporte de presión BPA1<br>a la computadora de supervisión</td>
    <td>El operador se conecta a la computadora de supervisión comandando el<br>reporte de la presión BPA1.</td>
    <td>La computadora de supervisión debe estar<br>conectada a la interfaz UART</td>
    <td>1. El operador envía el comando 'r' para inicial el reporte de la presión.<br>2. Se envía la presión BPA1 en un payload de JSON.3<br>3. El operador envía el comando 'R' para detener el reporte de la presión.         </td>
    <td>-</td>
  </tr>
</tbody></table>

**Tabla 4: subconjunto de casos de uso del sistema.**

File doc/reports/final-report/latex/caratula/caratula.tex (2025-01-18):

\begin{titlepage}

`\centering 

\vspace{1em}

\begin{center}
  \Large{\textbf{Universidad de Buenos Aires}}
  
  \Large{\textbf{Facultad de Ingeniería}}
  
  \Large{\textbf{86.65 Sistemas Embebidos}}  
\end{center}

\vspace{3em}

\centering \Large{Memoria del Trabajo Final:}

\centering \Large{\textbf{Sistema Carbonatador de cerveza}}

\vspace{3em}

\centering \Large{\textbf{Autor:}}

\centering {\Large{\textbf{Hernán Leandro Bailo}}}

\vspace{3em}

\centering \Large{Legajo: 97.841} 

\vfill

\centering \textit{Este trabajo fue realizado en la Ciudad de Buenos Aires entre Julio y Diciembre de 2024.}

\hrulefill

\end{titlepage}

%%% Local Variables:
%%% mode: latex
%%% TeX-master: "../main"
%%% End:

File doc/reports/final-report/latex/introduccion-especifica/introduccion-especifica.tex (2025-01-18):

\section{Requisitos}
En la tabla \ref{table:requisitos} se muestran los requisitos del sistema desarrollado.

\begin{table}[H]
\centering
\begin{tabular}{|c|l|l|}
\hline
\rowcolor[HTML]{EFEFEF} 
\textbf{Grupo}                                                                                  & \multicolumn{1}{c|}{\cellcolor[HTML]{EFEFEF}\textbf{ID}} & \multicolumn{1}{c|}{\cellcolor[HTML]{EFEFEF}\textbf{Descripción}}                 \\ \hline
                                                                                                & 1.1                                                      & Implementación de receta de carbonatación según ISA S88.                          \\ \cline{2-3} 
                                                                                                & 1.2                                                      & Inyección de CO2 mediante válvula solenoide (QMB1).                               \\ \cline{2-3} 
                                                                                                & 1.3                                                      & Disolución de CO2 mediante criba vibratoria accionada por motor eléctrico (MAA1). \\ \cline{2-3} 
\multirow{-4}{*}{Control del proceso}                                                           & 1.4                                                      & Monitoreo de presión (BPA1).                                                      \\ \hline
                                                                                                & 2.1                                                      & Comunicación con MCU.                                                             \\ \cline{2-3} 
                                                                                                & 2.2                                                      & Indicación de estado de receta.                                                   \\ \cline{2-3} 
                                                                                                & 2.3                                                      & Indicación de paso de receta.                                                     \\ \cline{2-3} 
                                                                                                & 2.4                                                      & Indicación de alarmas.                                                            \\ \cline{2-3} 
                                                                                                & 2.5                                                      & Indicación de presión BPA1.                                                       \\ \cline{2-3} 
\multirow{-6}{*}{HMI}                                                                           & 2.6                                                      & Botones de comando de receta: start, stop, hold, resume, reset.                   \\ \hline
                                                                                                & 3.1                                                      & Conexión con MCU.                                                                 \\ \cline{2-3} 
\multirow{-2}{*}{Sirena}                                                                        & 3.2                                                      & Configuración de la alerta sonora.                                                \\ \hline
                                                                                                & 4.1                                                      & Comunicación con MCU.                                                             \\ \cline{2-3} 
                                                                                                & 4.2                                                      & Comandos de receta: start, stop, hold, resume, reset.                             \\ \cline{2-3} 
                                                                                                & 4.3                                                      & Comando de reporte de presión BPA1.                                               \\ \cline{2-3} 
\multirow{-4}{*}{\begin{tabular}[c]{@{}c@{}}Computadora de\\ supervisión\end{tabular}}          & 4.4                                                      & Comando de ayuda al operador.                                                     \\ \hline
                                                                                                & 5.1                                                      & Alarma por sobrepresión cuando \(BPA1 > 4\,bar\).                                 \\ \cline{2-3} 
\multirow{-2}{*}{\begin{tabular}[c]{@{}c@{}}Sistema de alarmas\\ y enclavamientos\end{tabular}} & 5.2                                                      & Detención del proceso por sobrepresión cuando \(BPA1 > 4\,bar\).                  \\ \hline
                                                                                                & 6.1                                                      & Comunicación WiFi con MCU.                                                        \\ \cline{2-3} 
                                                                                                & 6.2                                                      & Implementación de servidor HTTP.                                                  \\ \cline{2-3} 
                                                                                                & 6.3                                                      & Indicación de estado de receta mediante HTML.                                     \\ \cline{2-3} 
                                                                                                & 6.4                                                      & Indicación de paso de receta.                                                     \\ \cline{2-3} 
                                                                                                & 6.5                                                      & Indicación de presión BPA1.                                                       \\ \cline{2-3} 
\multirow{-6}{*}{Servidor web}                                                                  & 6.6                                                      & Indicación de alarmas.                                                            \\ \hline
\end{tabular}
\caption{Requisitos del sistema automático.}
\label{table:requisitos}
\end{table}

\section{Casos de uso}
En las tablas \ref{table:caso-de-uso-1}, \ref{table:caso-de-uso-2} y \ref{table:caso-de-uso-3} se presentan tres casos de uso del sistema representativos de su funcionalidad.

\begin{table}[H]
\centering
\begin{tabular}{|
>{\columncolor[HTML]{EFEFEF}}l |l|}
\hline
\textbf{Caso de uso}       & Inicio de receta de carbonatación                                                                                                                                                        \\ \hline
\textbf{Descripción}       & El operador inicia la receta para carbonatar un barril de cerveza.                                                                                                                       \\ \hline
\textbf{Precondición}      & La receta debe estar en el estado Idle y el sistema no debe estar enclavado.                                                                                                             \\ \hline
\textbf{Flujo principal}   & \begin{tabular}[c]{@{}l@{}}1. El operador selecciona Start en el HMI.\\ 2. El sistema inicia la receta.\\ 3. Se inyecta \(CO_{2}\) y se agita el barril según el algoritmo.\end{tabular} \\ \hline
\textbf{Flujo alternativo} & \begin{tabular}[c]{@{}l@{}}Si se detecta \(BPA1 > 4\,bar\), se activa la alarma, se detiene el proceso y se\\ notifica al operador.\end{tabular}                                         \\ \hline
\end{tabular}
\caption{Caso de uso 1, inicio de la ejecución de la receta.}
\label{table:caso-de-uso-1}
\end{table}

\begin{table}[H]
\centering
\begin{tabular}{|
>{\columncolor[HTML]{EFEFEF}}l |l|}
\hline
\textbf{Caso de uso}       & Pausa y reanudación de receta                                                                                                                                                                    \\ \hline
\textbf{Descripción}       & El operador pausa temporalmente la receta en ejecución y luego la reanuda.                                                                                                                       \\ \hline
\textbf{Precondición}      & La receta debe estar en el estado Executing.                                                                                                                                                     \\ \hline
\textbf{Flujo principal}   & \begin{tabular}[c]{@{}l@{}}1. El operador selecciona Hold en el HMI.\\ 2. El sistema detiene la operación de los actuadores.\\ 3. Posteriormente, selecciona Resume para continuar.\end{tabular} \\ \hline
\textbf{Flujo alternativo} & \begin{tabular}[c]{@{}l@{}}Si la presión en el barril cambia mientras está pausado, \\ se realiza una notificación visual en el HMI.\end{tabular}                                                \\ \hline
\end{tabular}
\caption{Caso de uso 2, pausa y reanudación de receta}
\label{table:caso-de-uso-2}
\end{table}

\begin{table}[H]
\centering
\begin{tabular}{|
>{\columncolor[HTML]{EFEFEF}}l |l|}
\hline
\textbf{Caso de uso}       & Reporte de presión BPA1 a la computadora de supervisión.                                                                                                                                                                                             \\ \hline
\textbf{Descripción}       & \begin{tabular}[c]{@{}l@{}}El operador se conecta a la computadora de supervisión comandando el\\ reporte de la presión BPA1.\end{tabular}                                                                                                           \\ \hline
\textbf{Precondición}      & La computadora de supervisión debe estar conectada a la interfaz UART.                                                                                                                                                                               \\ \hline
\textbf{Flujo principal}   & \begin{tabular}[c]{@{}l@{}}1. El operador envía el comando 'r' para inicial el reporte de la presión.\\ 2. Se envía la presión BPA1 en un payload de JSON.\\ 3. El operador envía el comando 'R' para detener el reporte de la presión.\end{tabular} \\ \hline
\textbf{Flujo alternativo} & \multicolumn{1}{c|}{-}                                                                                                                                                                                                                               \\ \hline
\end{tabular}
\caption{Caso de uso 3, reporte de presión BPA1 a la computadora de supervisión a través del terminal serie.}
\label{table:caso-de-uso-3}
\end{table}

\section{Descripción de módulos utilizados}
En base a la arquitectura de control y los requisitos establecidos se decidió por utilizar los módulos que se describen a continuación.

\subsection{Módulo del microcontrolador}
Se utilizó como módulo microcontrolador la placa NUCLEO-F429ZI \cite{NUCLEO}, equipada con un microcontrolador STM32F429ZI, figura \ref{fig:nucleo}.

Los principales puntos tenidos en cuenta para la adopción de esta placa son:
\begin{itemize}
\item Rendimiento y recursos: El STM32F429ZI incluye un núcleo ARM Cortex-M4 de alto rendimiento con capacidad de punto flotante, ideal para realizar cálculos en tiempo real y ejecutar múltiples tareas simultáneamente.
\item Periféricos integrados: La placa cuenta con una amplia gama de periféricos como UART, SPI, ADC y GPIO, que permiten una integración eficiente con los sensores y actuadores del sistema.
\item Compatibilidad con herramientas de desarrollo: La placa es compatible con Mbed OS y herramientas como STM32CubeIDE, lo que facilita el desarrollo del software.
\item Documentación y soporte: La disponibilidad de documentación detallada simplifica el proceso de implementación y resolución de problemas.
\end{itemize}

\begin{figure}[H]
  \centering
  
  \caption{NUCLEO-F429ZI.}
  \label{fig:nucleo}
\end{figure}

\subsection{Módulo del display táctil}
Para la implementación del HMI se utilizó el módulo display \cite{LCD} con pantalla LCD TFT de 2.4' y drivers de hardware ILI9341 y XPT2046 que se muestra en la figura \ref{fig:hmi}.

El comando gráfico del LCD se realiza con el hardware ILI9341 a través de una comunicación SPI y el comando de la interacción táctil con el hardware XPT2046 también a través de una comunicación SPI.

\begin{figure}[H]
  \centering
  
  \caption{Modulo display táctil.}
  \label{fig:hmi}
\end{figure}

\subsection{Módulo Wi-Fi}
Para la implementación de la comunicación con la computadora de supervisión a través de un navegador web se utiliza el módulo Wi-Fi ESP01 \cite{ESP01} de la figura \ref{fig:esp01}.

Este módulo se comunica con el microcontrolador a través de una interfaz UART y la configuración del mismo se realiza a través de comandos AT.

\begin{figure}[H]
  \centering
  
  \caption{Modulo ESP01.}
  \label{fig:esp01}
\end{figure}

\subsection{Buzzer}
Para las indicaciones auditivas se utiliza el buzzer pasivo KY-006 que se muestra en la figura \ref{fig:buzzer}. El dispositivo se activa enviando una señal PWM al terminal de entrada.

\begin{figure}[H]
  \centering
  
  \caption{Buzzer}
  \label{fig:buzzer}
\end{figure}

\subsection{Módulo de alimentación}
Para la alimentación de los módulos de display, Wi-Fi y el buzzer se utiliza el módulo MB102 que se muestra en la figura \ref{fig:mb102}. El dispositivo genera \(3.3\,V\) al conectar el USB de entrada a \(5\,V\).

\begin{figure}[H]
  \centering
  
  \caption{Módulo de alimentación MB102.}
  \label{fig:mb102}
\end{figure}

%%% Local Variables:
%%% mode: latex
%%% TeX-master: "../main"
%%% End:

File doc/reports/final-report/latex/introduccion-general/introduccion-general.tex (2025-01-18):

\section{Objetivo}

El objetivo del proyecto es desarrollar un sistema automatizado y modular de un equipo carbonatador existente para la carbonatación de cerveza en barriles, capaz de garantizar calidad, precisión y consistencia en el proceso, bajo estándares industriales como ISA S88 \cite{BRAN}, y con capacidad de integración en sistemas de gestión mediante comunicación abierta.

\section{Equipo}
El equipo carbonatador a automatizar esta diseñado a medida para una planta de bajo nivel de producción. En la figura \ref{fig:p-and-id} se muestra un diagrama P\&ID con tags en formato IEC 81346-2 \cite{IEC}.

El sistema consiste en untanque de \(CO_{2}\) conectado a un barril de cerveza a través de la válvula solenoide QMB1. El barril se encuentra montado sobre una criba vibratoria que se acciona mediante el motor eléctrico MAA1. La presión interna del barril se mide con el transmisor BPA1.

\begin{figure}[H]
  \centering
  
  \caption{P\&ID del carbonatador}
  \label{fig:p-and-id}
\end{figure}

\section{Descripción del proceso}
En el proceso de elaboración de la cerveza una de las últimas etapas es la carbonatación, donde se incorpora dióxido de carbono a líquido para crear efervescencia, realzar el sabor, conservar la cerveza y otros propósitos. En el caso actual la carbonatación se realiza artificialmente mediante la incorporación forzada del gas.

El procedimiento se basa en la iteración de las siguientes dos fases, estructuradas según el patrón de diseño ISA S88 \cite{BRAN}:

\begin{itemize}
\item Inyección de CO2: Accionando la válvula solenoide (normalmente cerrada) (QMB1) se inyecta CO2 al barril de cerveza. La cantidad de gas inyectado se mide a través de la presión del barril (BPA1).
\item Disolución del CO2: Encendiendo la criba vibratoria (MAA1) se agita la cerveza y se favorece la disolución del CO2. El grado de disolución se mide indirectamente a través de la presión del barril (BPA1). A medida que el CO2 se diluye en la cerveza BPA1 decrece y se establece en un determinado valor. Se asume que se completó la disolución cuando dos muestras sucesivas de BPA1 con una separación de 1s difieren en menos de 10 mbar.
\end{itemize}

\subsection{Receta}
La receta que se requiere automatizar para lograr la carbonatación completa de un barril estándar se describe a continuación en pasos numerados y se muestra gráficamente en el diagrama de flujo de la figura \ref{fig:receta-de-carbonatacion}.

\begin{enumerate}
\item Se inyectan 3 bares de \(CO_{2}\) al barril accionando QMB1 hasta que \(BPA1 = 3\,bar\).
\item Se diluye el \(CO_{2}\) encendiendo la criba vibratoria. Si una vez diluido el gas se mide \(0.9\,bar < BPA1 < 1\,bar\) entonces se finaliza la receta con el barril correctamente carbonatado, sino si \(BPA1 < 0.9\,bar\) se pasa al paso 3.
\item Se inyectan 2 bares de \(CO_{2}\).
\item Se diluye el \(CO_{2}\) y si \(0.9\,bar < BPA1 < 1\,bar\) se finaliza satisfactoriamente la receta, sino si \(BPA1 < 0.9\,bar\) se pasa al paso 5.
\item Se inyecta 1 bar de \(CO_{2}\).
\item Se diluye el CO2 y si \(0.9\,bar < BPA1 < 1\,bar\) se finaliza satisfactoriamente la receta, sino si \(BPA1 < 0.9\,bar\) se repiten los pasos 5 y 6 indefinidamente.
\end{enumerate}

En los pasos 2, 4 y 6 la condición \(BPA1 > 1\,bar\) detiene la receta dado que no debería producirse si el sistema funciona adecuadamente. Se debe revisar el equipo.

\begin{figure}[H]
  \centering
  
  \caption{Diagrama de flujo de la receta de carbonatación.}
  \label{fig:receta-de-carbonatacion}
\end{figure}

\subsection{Interacción del operador}
La operación del sistema se basa en la ejecución de la receta de carbonatación, siguiendo el patrón de diseño de manufactura flexible ISA S88 \cite{BRAN}.

El operador controla el estado de la receta a través de los siguientes comandos:

\begin{itemize}
\item Start: inicia la receta.
\item Stop: detiene la receta.
\item Hold: pausa la receta.
\item Resume: reanuda la receta.
\item Reset: reinicia la receta.
\end{itemize}

Los comandos se encuentran ligados con los estados de la receta de acuerdo al diagrama de estados de la figura \ref{fig:estados-de-la-receta}.

\begin{figure}[H]
  \centering
  
  \caption{Diagrama de estados de la ejecución de la receta de carbonatación.}
  \label{fig:estados-de-la-receta}
\end{figure}
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

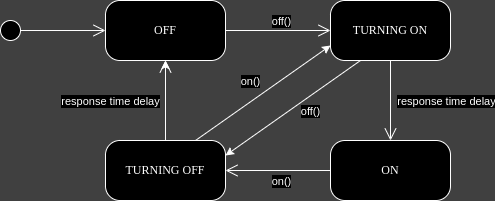
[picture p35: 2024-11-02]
doc/design/classes/SolenoidValve/state-diagram-dark.png

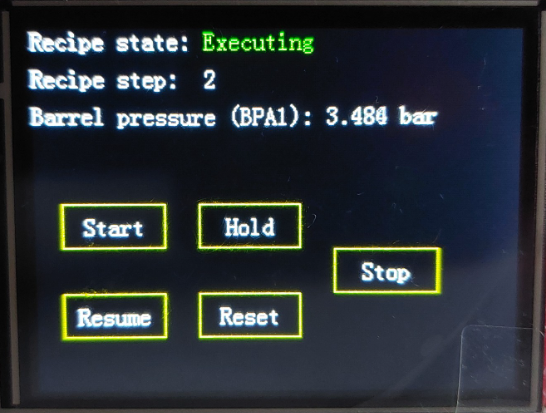
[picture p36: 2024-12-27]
doc/reports/final-report/markdown/img/hmi-home.png

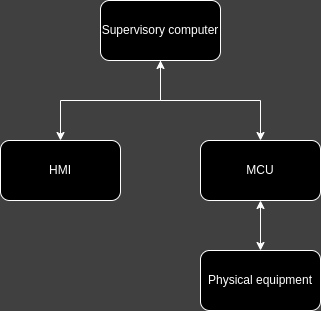
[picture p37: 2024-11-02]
doc/architecture/hardware-architecture-dark.png

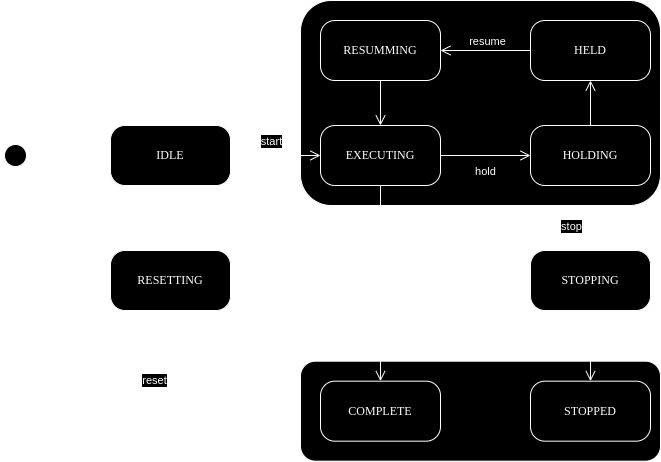
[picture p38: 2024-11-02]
doc/design/classes/CarbonationRecipe/recipe-state-diagram-dark.png

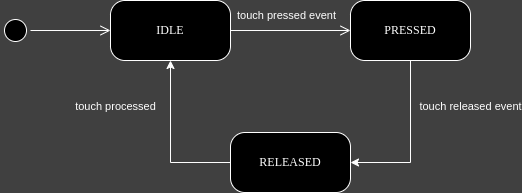
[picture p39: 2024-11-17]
doc/design/classes/HMI/touch-state-diagram-dark.png

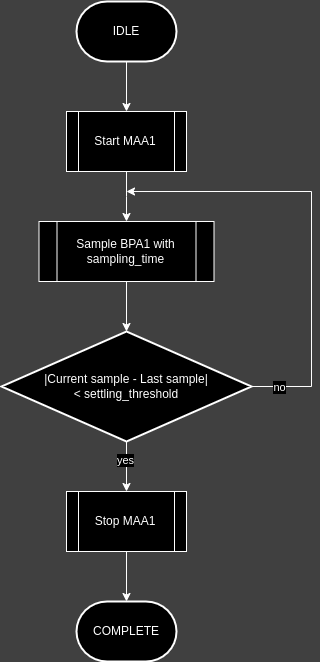
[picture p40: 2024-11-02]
doc/design/classes/CO2Dissolver/flowchart-diagram-dark.png

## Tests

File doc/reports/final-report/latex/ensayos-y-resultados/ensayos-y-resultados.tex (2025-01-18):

\section{Pruebas funcionales del hardware}
Las pruebas funcionales del hardware se realizaron por módulos.

\subsection{Módulo Wi-Fi ESP01}
Se conectó el módulo a la placa y en paralelo un analizador de protocolos para verificar el correcto envío de comandos y la recepción de respuestas.

\subsection{Módulo HMI}
Se conectó el módulo a la placa y se realizó la calibración del display mediante la graficación de puntos.
Adicoinalmente se conectó un analizador de protocolos en los pines de comunicación ambos SPI para verificar el correcto envío de comandos y la recepción de respuestas.

\subsection{Módulo buzzer}
Se conectó el buzzer al terminal de masa y se le envío una señal PWM con la placa nucleo verificando el correcto funcionamiento.

\subsection{Transmisor de presión}
El transmisor de presión se simuló mediante un potenciometro de \(50\,k\Omega\). Se conectó el mismo a los \(3.3\,V\) generados por la placa y se verificó que el valor medido por el objeto AnalogIn sea consistente con las mediciones realizadas con multímetro.

\subsection{Módulo de alimentación}
Se conectó el módulo de alimentación al protoboard y a la fuente de \(5\,V\). Se verificó mediante una medición de voltímetro que la tensión generada era de \(3.3\,V\).

\subsection{Motor MAA1 y válvula solenoide QMB1}
Para demostrar el correcto funcionamiento de las salidas digitales correspondientes al motor MAA1 y QMB1 se conectaron sus salidas a los LEDs 1 y 2 de la placa NUCLEO.

\subsection{Pruebas funcionales del firmware}
Las pruebas funcionales del firmware se realizaron en conjunto con las distintas pruebas para los módulos de hardware.

La lógica de la receta se verificó mediante el uso del debugger.

\subsection{Pruebas de integracion}
Las pruebas de integración realizadas se encuentran en formato de video en \cite{PDI}.

Se verificó:

\begin{itemize}
\item Disposición del hardware.
\item Lógica de la receta y respuesta a comandos.
\item Comandos mediante la computadora de supervisión por terminal serie.
\item Monitoreo mediante el servidor web.
\item Alarmas y enclavamientos.
\end{itemize}

\subsection{Cumplimiento de requisitos}
En la tabla \ref{table:cumplimiento-requisitos} se presenta la evaluación del cumplimiento de los requisitos iniciales de la tabla \ref{table:requisitos}. Se evaluó a el estado actual de cada uno indicando en verde aquellos que ya fueron cumplidos y en rojo los requerimientos no cumplidos.

% Please add the following required packages to your document preamble:
% \usepackage{multirow}
% \usepackage[table,xcdraw]{xcolor}
% Beamer presentation requires \usepackage{colortbl} instead of \usepackage[table,xcdraw]{xcolor}
\begin{table}[H]
\centering
\begin{tabular}{|c|l|
>{\columncolor[HTML]{32CB00}}l |}
\hline
\cellcolor[HTML]{EFEFEF}\textbf{Grupo}                                                          & \multicolumn{1}{c|}{\cellcolor[HTML]{EFEFEF}\textbf{ID}} & \multicolumn{1}{c|}{\cellcolor[HTML]{EFEFEF}\textbf{Descripción}}                \\ \hline
                                                                                                & 1.1                                                      & Implementación de receta de carbonatación según ISA S88                          \\ \cline{2-3} 
                                                                                                & 1.2                                                      & Inyección de CO2 mediante válvula solenoide (QMB1)                               \\ \cline{2-3} 
                                                                                                & 1.3                                                      & Disolución de CO2 mediante criba vibratoria accionada por motor eléctrico (MAA1) \\ \cline{2-3} 
\multirow{-4}{*}{Control del proceso}                                                           & 1.4                                                      & Monitoreo de presión (BPA1)                                                      \\ \hline
                                                                                                & 2.1                                                      & Comunicación con MCU                                                             \\ \cline{2-3} 
                                                                                                & 2.2                                                      & Indicación de estado de receta                                                   \\ \cline{2-3} 
                                                                                                & 2.3                                                      & Indicación de paso de receta                                                     \\ \cline{2-3} 
                                                                                                & 2.4                                                      & Indicación de alarmas                                                            \\ \cline{2-3} 
                                                                                                & 2.5                                                      & Indicación de presión BPA1                                                       \\ \cline{2-3} 
\multirow{-6}{*}{HMI}                                                                           & 2.6                                                      & Botones de comando de receta: start, stop, hold, resume, reset                   \\ \hline
                                                                                                & 3.1                                                      & Conexión con MCU                                                                 \\ \cline{2-3} 
\multirow{-2}{*}{Sirena}                                                                        & 3.2                                                      & Configuración de la alerta sonora                                                \\ \hline
                                                                                                & 4.1                                                      & Comunicación con MCU                                                             \\ \cline{2-3} 
                                                                                                & 4.2                                                      & Comandos de receta: start, stop, hold, resume, reset                             \\ \cline{2-3} 
                                                                                                & 4.3                                                      & Comando de reporte de presión BPA1                                               \\ \cline{2-3} 
\multirow{-4}{*}{\begin{tabular}[c]{@{}c@{}}Computadora de\\ supervisión\end{tabular}}          & 4.4                                                      & Comando de ayuda al operador                                                     \\ \hline
                                                                                                & 5.1                                                      & Alarma por sobrepresión cuando BPA1 \textgreater 4 bar                           \\ \cline{2-3} 
\multirow{-2}{*}{\begin{tabular}[c]{@{}c@{}}Sistema de alarmas\\ y enclavamientos\end{tabular}} & 5.2                                                      & Detención del proceso por sobrepresión cuando BPA1 \textgreater 4 bar            \\ \hline
                                                                                                & 6.1                                                      & Comunicación WiFi con MCU                                                        \\ \cline{2-3} 
                                                                                                & 6.2                                                      & Implementación de servidor HTTP                                                  \\ \cline{2-3} 
                                                                                                & 6.3                                                      & Indicación de estado de receta mediante HTML                                     \\ \cline{2-3} 
                                                                                                & 6.4                                                      & Indicación de paso de receta                                                     \\ \cline{2-3} 
                                                                                                & 6.5                                                      & Indicación de presión BPA1                                                       \\ \cline{2-3} 
\multirow{-6}{*}{Servidor web}                                                                  & 6.6                                                      & Indicación de alarmas                                                            \\ \hline
\end{tabular}
\caption{Estado de los requisitos.}
\label{table:cumplimiento-requisitos}
\end{table}

\section{Documentación del desarrollo realizado}

\begin{table}[H]
\centering
\begin{tabular}{|l|l|}
\hline
\rowcolor[HTML]{EFEFEF} 
\multicolumn{1}{|c|}{\cellcolor[HTML]{EFEFEF}\textbf{Elemento}} & \multicolumn{1}{c|}{\cellcolor[HTML]{EFEFEF}\textbf{Referencia}} \\ \hline
Presentación del proyecto                                       & Capítulo 1                                                       \\ \hline
Listado de requisitos                                           & Tabla 2.1                                                        \\ \hline
Casos de uso del proyecto                                       & Tablas 2.2 a 2.3                                                 \\ \hline
Diagrama en bloques del sistema                                 & Figura 3.1                                                       \\ \hline
Lista de señales                                                & Tabla 3.1                                                        \\ \hline
Implementación del hardware                                     & Sección 3.1                                                      \\ \hline
Módulos de software                                             & Sección 3.2                                                      \\ \hline
Repositorio                                                     & \textbackslash{}cite\{REPO\}                                     \\ \hline
Cumplimiento de requisitos                                      & Tabla 4.1                                                        \\ \hline
Conclusiones finales                                            & Capítulo 5                                                       \\ \hline
\end{tabular}
\caption{Elementos del sumario del sistema automático para el sistema de carbonatación de cerveza.}
\label{table:documentacion}
\end{table}

%%% Local Variables:
%%% mode: LaTeX
%%% TeX-master: "../main"
%%% End:

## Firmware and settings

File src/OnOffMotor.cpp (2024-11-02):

#include "OnOffMotor.h"

using namespace std::chrono;

/**
 *  @param on_actuating_signal_pin the actuating signal DO pin.
 *  @param response_time the motor response time.
 */
OnOffMotor::OnOffMotor(PinName on_actuating_signal_pin, std::chrono::seconds response_time)
  : on_actuating_signal(on_actuating_signal_pin, false), response_time(response_time), state(State::OFF)
{
  
}

/**
 * @return the solenoid valve state.
 */
OnOffMotor::State OnOffMotor::on()
{

  switch (state) {
    
  case State::OFF: 
    on_actuating_signal = true;
    timer.start();    
    state = State::TURNING_ON;
    break;

  case State::ON:
    break ;
    
  case State::TURNING_OFF:
    on_actuating_signal = true ;
    timer.reset() ;
    state = State::TURNING_ON ;
    break ;
    
  case State::TURNING_ON:
    
    if (timer.elapsed_time() > response_time) {
      timer.stop();
      timer.reset() ;
      state = State::ON ;
    }
    
    break ;
    
  }

  return state ;
  
}

/**
 * @return the solenoid valve state.
 */
OnOffMotor::State OnOffMotor::off()
{

  switch (state) {

  case State::OFF:
    break ;
    
  case State::ON:
    on_actuating_signal = false ;
    timer.start() ;
    state = State::TURNING_OFF ;
    break ;
    
  case State::TURNING_OFF:

    if (timer.elapsed_time() > response_time) {
      timer.stop();
      timer.reset() ;
      state = State::OFF ;
    }
    
    break ;
    
  case State::TURNING_ON:
    on_actuating_signal = false ;
    timer.reset() ;
    state = State::TURNING_OFF ;
    break ;
    
  }

  return state ;
  
}

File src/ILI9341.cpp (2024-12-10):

#include "ILI9341.h"
#include "mbed.h"
#include <cstdint>

/**

 * ILI9341 is initialized with the following parametrization:
 * - 16 bits colors
 * - Memory access control: BGR to RGB.
 */
ILI9341::ILI9341(PinName mosi_pin, PinName miso_pin, PinName sckl_pin, PinName cs_pin, PinName dcx_pin, PinName resx_pin)
  : spi(mosi_pin, miso_pin, sckl_pin), cs(cs_pin, false), dcx(dcx_pin, false), resx(resx_pin, true)
{

  spi.format(8, 0);        // SPI frame of 8 bits and clock polarity and phase mode 0.
  spi.frequency(10000000); // 1 MHz
  
  powerOn();

}

void ILI9341::setPixel(uint16_t x, uint16_t y, Color color)
{
  
  setFrameMemoryAreaAddress(x, x, y, y);
  
  writeFrameMemoryArea(&color, 1);

}

/**
 *  A frame area is a rectangular area of the display that is specified from its pixel
 *  of origin and extends downward and to the right.
 *  The pixel of origin is the one corresponding to the upper left corner of the frame area.
 *  The frame area data is passed as an array of colors where the elements correspond to the
 *  path from left to right and top to bottom of the pixels of the frame area, starting with
 *  the pixel of origin.
 *
 *  Frame area  <--  Frame area data array
 *  [A, B, C]         [A, B, C, D, E, F]
 *  [D, E, F]
 * 
 *  @pre This function does NOT check arguments size consistency, i.e. data array can be longer or shorter than the specified frame area. It is up to the user to check the sizes.
 *  
 *  @param x the x pixel coordinate of the upper-left corner of the frame area.
 *  @param y the y pixel cooordinate of the upper-left corner of the frame area.
 *  @param width the frame area width in pixels.
 *  @param height the frame height area in pixels.
 *  @param data the frame area color data.
 */ 
void ILI9341::drawImage(uint16_t x, uint16_t y, uint16_t width, uint16_t height, const Color* data)
{
  
  setFrameMemoryAreaAddress(x, x + width - 1, y, y + height - 1);
  writeFrameMemoryArea(data, width * height);

}
 
/** @brief Fills the screen with color. 
 *
 *  @todo Refactorize, improve performance and FIX display dimensions hardcoding.
*/
void ILI9341::fillScreen(Color color)
{
  
  Color patch[2 * 320];
  
  for (uint16_t i = 0; i < 2 * 320; ++i) {
      patch[i] = color;
  }
  
  for (uint16_t y = 0; y < 320; y += 2) {

    for (uint16_t x = 0; x < 240; x += 240) {
      drawImage(x, y, 320, 2, patch);
    }

  }

}

/**
 *  @note The line includes the endpointes, i.e. extends over pixels (@p x0, @p y)
 *  to (@p x1, @p y). For example if @p x0 = 0 and @p x1 = 2, then pixels
 *  (0, @p y), (1, @p y), (2, @p y) are setted.
 *
 *  @param[in] x the x pixel coordinate of the left line endpoint.
 *  @param[in] y the y pixel coordinate of the left line endpoint.
 *  @param[in] length the length in pixels of the line.
 *
 *  @pre @p x0 ≤ @p x1
 *
 *  @todo Refactorize, improve performance and FIX display dimensions hardcoding.
*/
void ILI9341::drawHLine(uint16_t y, uint16_t x0, uint16_t x1, Color color)
{
  
  Color buf[320]; // TODO: This buffer is used in many functions, maybe it can be part of the class.

  uint16_t length = x1 - x0 + 1;
  
  for (uint16_t i = 0; i < length; ++i) {
      buf[i] = color;
  }

  setFrameMemoryAreaAddress(x0, x1, y, y);
  writeFrameMemoryArea(buf, length);
  
}

/**
 *  @note The line includes the endpoints, i.e. extends over pixels (@p x, @p y0)
 *  to (@p x, @p y1). For example if @p y0 = 0 and @p y1 = 2, then pixels
 *  (@p x, 0), (@p x, 1), (@p x, 2) are setted.
 *
 *  @param[in] x the x pixel coordinate of the left line endpoint.
 *  @param[in] y the y pixel coordinate of the left line endpoint.
 *  @param[in] length the length in pixels of the line.
 *
 *  @pre @p y0 ≤ @p y1
 *
 *  @todo Refactorize, improve performance and FIX display dimensions hardcoding.
*/
void ILI9341::drawVLine(uint16_t x, uint16_t y0, uint16_t y1, Color color)
{
  
  Color buf[320]; // TODO: This buffer is used in many functions, maybe it can be part of the class.

  uint16_t length = y1 - y0 + 1;
  
  for (uint16_t i = 0; i < length; ++i) {
      buf[i] = color;
  }  

  setFrameMemoryAreaAddress(x, x, y0, y1);
  writeFrameMemoryArea(buf, length);
  
}

void ILI9341::drawRectangle(uint16_t x0, uint16_t y0, uint16_t x1, uint16_t y1, Color color)
{

  drawHLine(y0, x0, x1, color); // Bottom edge
  drawHLine(y1, x0, x1, color); // Top    edge 
  drawVLine(x0, y0, y1, color); // Left   edge
  drawVLine(x1, y0, y1, color); // Right  edge

}

/** @brief Fills the screen with color. 
 *
 *  @todo Refactorize, improve performance and FIX display dimensions hardcoding.
*/
void ILI9341::powerOn()
{
  
  ThisThread::sleep_for(1ms); // NOTE: Duration of "After Powered ON" reset, see [1] page 228.

  reset(); // Hardware reset

  setMemoryAccessControl(0xE8); // MX | MY | MV | BGR
  setPixelFormat(0x05);         // MCU 16 bits pixel colors
  
  exitSleepMode();
 
  turnDisplayOn();

}


/** 
 *  @brief Performs a hardware reset.
 *  @note This method has an execution time of approximately 121 ms.
 */
void ILI9341::reset()
{

  resx = false;
  ThisThread::sleep_for(1ms); // NOTE: Minimum reset pulse duration, see [1] page 230.
  resx = true;
  ThisThread::sleep_for(120ms); // NOTE: Duration of hardware resseting, see [1] page 230, NOTE 3.

}

void ILI9341::exitSleepMode()
{

  writeCommand(SLEEP_OUT);
  ThisThread::sleep_for(5ms); // NOTE: Time for the supply voltages and clock
                              // circuits to stabilize, see [1] page 101.  
}

void ILI9341::setPixelFormat(uint8_t parameter)
{

  writeCommand(PIXEL_FORMAT_SET);
  writeParameter(parameter);
  
}

void ILI9341::turnDisplayOn()
{

  writeCommand(DISPLAY_ON);
  
}

void ILI9341::writeFrameMemoryArea(const Color* data, uint32_t data_length)
{

  writeCommand(MEMORY_WRITE);

  for (uint32_t i = 0; i < data_length; ++i) {
    writeParameter(data[i] >> 8);     // NOTE: if 18 bits colors need to be implemented
    writeParameter(data[i] & 0x00FF); // then 3 bytes need to be sent.
  }
  
}

void ILI9341::setFrameMemoryAreaAddress(uint16_t sc, uint16_t ec, uint16_t sp, uint16_t ep)
{

  setColumnAddress(sc, ec);
  setPageAddress(sp, ep);

}

/**
 *  Set the column range of frame memory where MCU can access.
 *
 *  Parameter ranges:
 *
 *  If display is in normal mode (MADCTL[5] = '0'):
 *    0 < sc < 239
 *    0 < ec < 319
 *
 *  If display is in reverse mode (MADCTL[5] = '1'):
 *    0 < sc < 319
 *    0 < ec < 239
 *
 *  @note Parameters out of range will be ignored.
 *
 *  @param[in] sc start column line number.
 *  @param[in] ec end column line number.
 */
void ILI9341::setColumnAddress(uint16_t sc, uint16_t ec)
{

  writeCommand(COLUMN_ADDRESS_SET);
  writeParameter(sc >> 8);
  writeParameter(sc & 0x00FF);
  
  writeParameter(ec >> 8);
  writeParameter(ec & 0x00FF);
  
}
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

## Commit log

2024-09-14 Initiate development of Solenoid valve control module
2024-09-17 Add pressure transmitter control module
2024-09-17 Refactorize solenoid valve control module
2024-09-17 Add on off motor control module
2024-10-10 Fix state machine timeout transitions logic
    [SolenoidValve.cpp]
2024-10-25 Implement ILI9341 hardware driver
2024-11-02 Add circuit diagram
    [circuit-diagram.kicad_pcb, circuit-diagram.kicad_sch]
2024-11-02 Add documentation
    [circuit-diagram.kicad_pcb, circuit-diagram.kicad_sch]
2024-11-11 Change pin names in the constructor.
2024-11-30 Remove led backlight DO
    Now the backlight led pin is fixed to 3.3 V.
    [ILI9341.cpp]
2024-11-30 Modify the pin connections
2024-11-30 Modify test pin connection
2024-12-09 Fix stackoverflow in fillScreen()
    [ILI9341.cpp]
2025-01-18 Add recipe flow diagrams
2025-01-18 Add flow diagram in drawio
